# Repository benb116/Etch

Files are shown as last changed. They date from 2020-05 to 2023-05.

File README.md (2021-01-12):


# Etch

Etch is an auto-drawing digital Etch a Sketch built on top of a Raspberry Pi. Stepper motors mounted under a television turn 3D printed knobs to match the drawing motion on the screen. The knobs can also be turned by hand to manually draw on the display.

This repository contains the following:

* 3D models of the shell, knobs, and other support pieces
* Altium PCB design files and Gerber files for the custom circuit boards
* RPi files for the server and motor/sensor integration
* Python scripts for generating art files from images

## About

### Hardware

Etch is built around a Raspberry Pi connected to a TV and two stepper motors. The Pi is connected to a custom breakout board that links with two other custom boards mounted to the back of the motors.

The motor boards serve two functions:

1. **AUTO Mode** - Take in step and direction signals from the breakout board and route them to the onboard stepper driver.
2. **MANUAL Mode** - Sense the orientation of a diametrically polarized magnet on the back of the motor axis. The motor position is then sent to the Pi to monitor the user's input.

The motors, shaft couplers, and knobs are mounted to two brackets that are adhered to the TV. 3D printed shell pieces are connected to an aluminum extrusion frame and wrapped in red vinyl.

Read more about [ME work](https://github.com/benb116/Etch/tree/master/ME) and [EE work](https://github.com/benb116/Etch/tree/master/EE).

### Software

The Pi runs a Python webserver that integrates with the motors and sensors. The server communicates with a webpage running in a browser that is displayed on the screen. A websocket connection passes information back and forth about art data, timing, and user input. In AUTO Mode, the server also runs through a script of artwork to display.

Art files contain the lists of points in order of travel. They also include information about drawing speed and knob rotation rates. These files can be generated with different methods:

* [ImageGen.py](https://github.com/benb116/Etch/blob/master/Art/ImageGen.py) - Take a full image and generate a path that traces contours and fills in darker regions.
* [PathFinder.py](https://github.com/benb116/Etch/blob/master/Art/pathfinder.py) - Identifies the path in a single line drawing
* DIY - You can use any method that outputs a series of line segments

Read more about the [Pi](https://github.com/benb116/Etch/tree/master/rPi) code and [Art](https://github.com/benb116/Etch/tree/master/Art) code.

## Further work

### Hardware

- [ ] Upgrade and fix the custom PCBs
- [ ] Add user input to toggle between AUTO and MANUAL

### Software

- [ ] Improve artwork generation algorithms
- [ ] Develop a show script
- [ ] Add support for arcs and splines
- [x] Improve webpage performance
- [x] Create standalone site with artwork

### Artwork

- [ ] Integrate Open Street Map
- [ ] Math and geometry
- [ ] Add support for different hatching schemes

## Acknowledgements

A big thanks to many people and organizations for their help and advice on this project.

* Everyone at [Bresslergroup](https://www.bresslergroup.com/), especially John, Jason, Steve, Nick, and Mike
* [Evil Mad Scientist](https://wiki.evilmadscientist.com/StippleGen)
* [Andrew Brooks](https://brooksandrew.github.io/simpleblog/articles/intro-to-graph-optimization-solving-cpp/)
* [Sunny Days](http://sunnybala.com/2018/09/10/python-etch-a-sketch.html)
* [Adrian Rosebrock](https://www.pyimagesearch.com/2015/04/06/zero-parameter-automatic-canny-edge-detection-with-python-and-opencv/)
* [Joe Freeman](https://web.archive.org/web/20140918131540/http://joefreeman.co.uk/blog/2009/09/lineographic-interpretations-of-images-with-an-etch-a-sketch/)
* [MIT](http://web.mit.edu/urban_or_book/www/book/chapter6/6.4.4.html)

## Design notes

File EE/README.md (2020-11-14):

# Electrical Hardware

Along with a Raspberry Pi, Etch utilizes two unique custom PCBs to route signals and power to various components.

1. Motor Board - Mounted to the back of each stepper motor, this PCB has a stepper motor driver to control the knob and a magnetic encoder to read the knob's position.
2. Breakout board - Mounted in the center of the TV, this PCB routes signals from the Pi to the correct board. It also distributes motor power.

## Motor Board
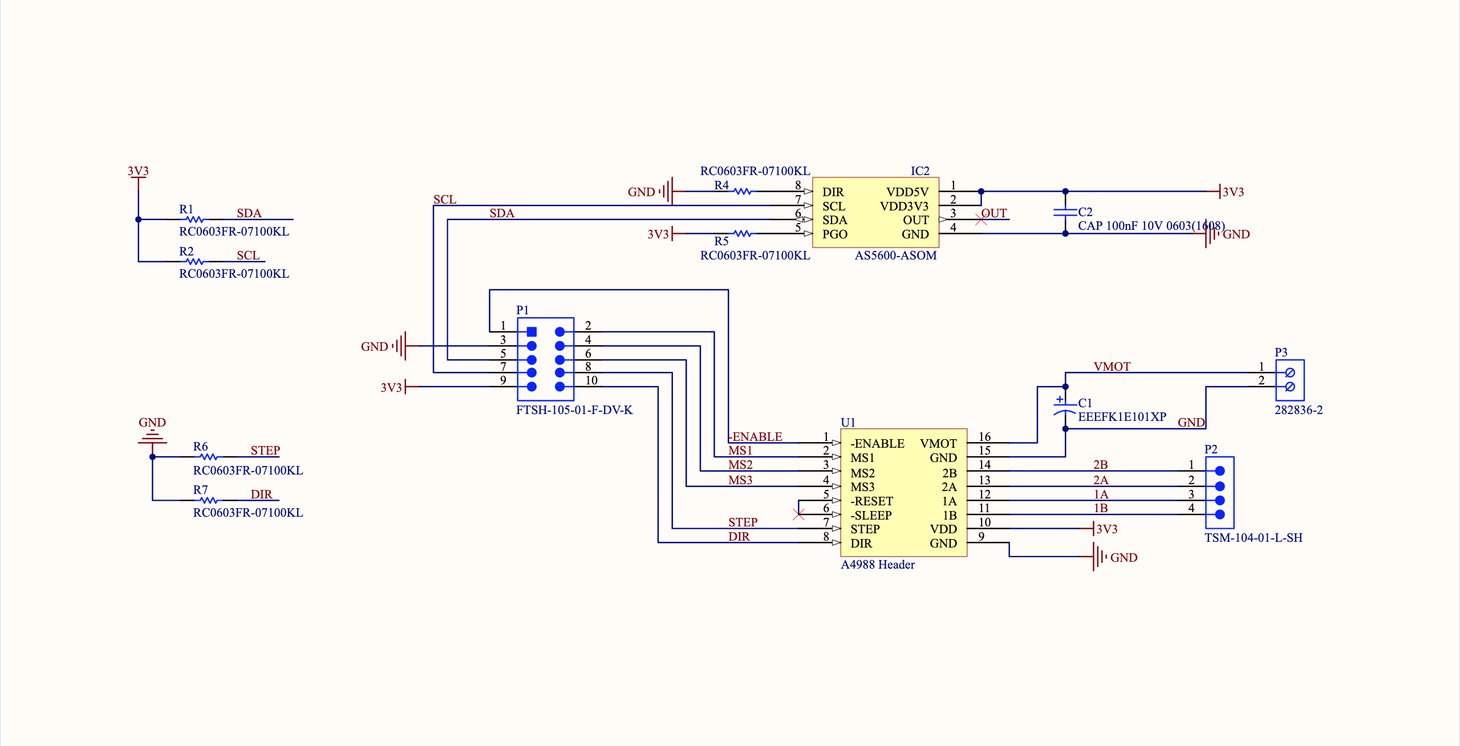
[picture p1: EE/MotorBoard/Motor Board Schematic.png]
Schematic


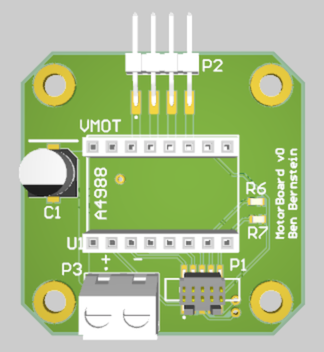
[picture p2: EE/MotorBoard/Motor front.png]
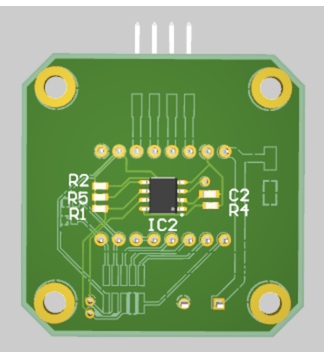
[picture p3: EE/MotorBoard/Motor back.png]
RenderBack


The Motor Board is designed to fit on the back of a standard NEMA-17 stepper motor. It accepts power and a 10-pin signal cable from the Breakout Board. The signals are:

1. **-ENABLE** | *Active low* | Pull this pin high to disable the motor (used in MANUAL mode)
2. **MS1** | *Pulled low* | Microstepping control pin 1
3. **GND**
4. **MS2** | *Pulled low* | Microstepping control pin 2
5. **SDA** | *Pulled high* | Encoder I2C Data pin
6. **MS3** | *Pulled low* | Microstepping control pin 3
7. **SCL** | *Pulled high* | Encoder I2C Clock pin
8. **STEP** | *Pulled low* | Step pulse pin
9. **3v3**
10. **DIR** | *Pulled low* | Direction control pin

Along with support components and connectors, the PCB has two main parts:

1. Headers that match an A4988 stepper motor driver (or similar) on the top layer
2. An [AS5600 magnetic rotary position sensor](https://ams.com/as5600) on the bottom layer. The sensor is centered over the motor axle which has a [diametrically polarized magnet](https://www.kjmagnetics.com/magdir.asp) glued to it. As the motor turns, the magnetic field rotates and is read by the sensor.
	- Note: Data is read from the sensor over I2C. The sensor has a fixed I2C address, so a 2-channel i2c bus multiplexer is required (see Breakout Board)

## Breakout Board
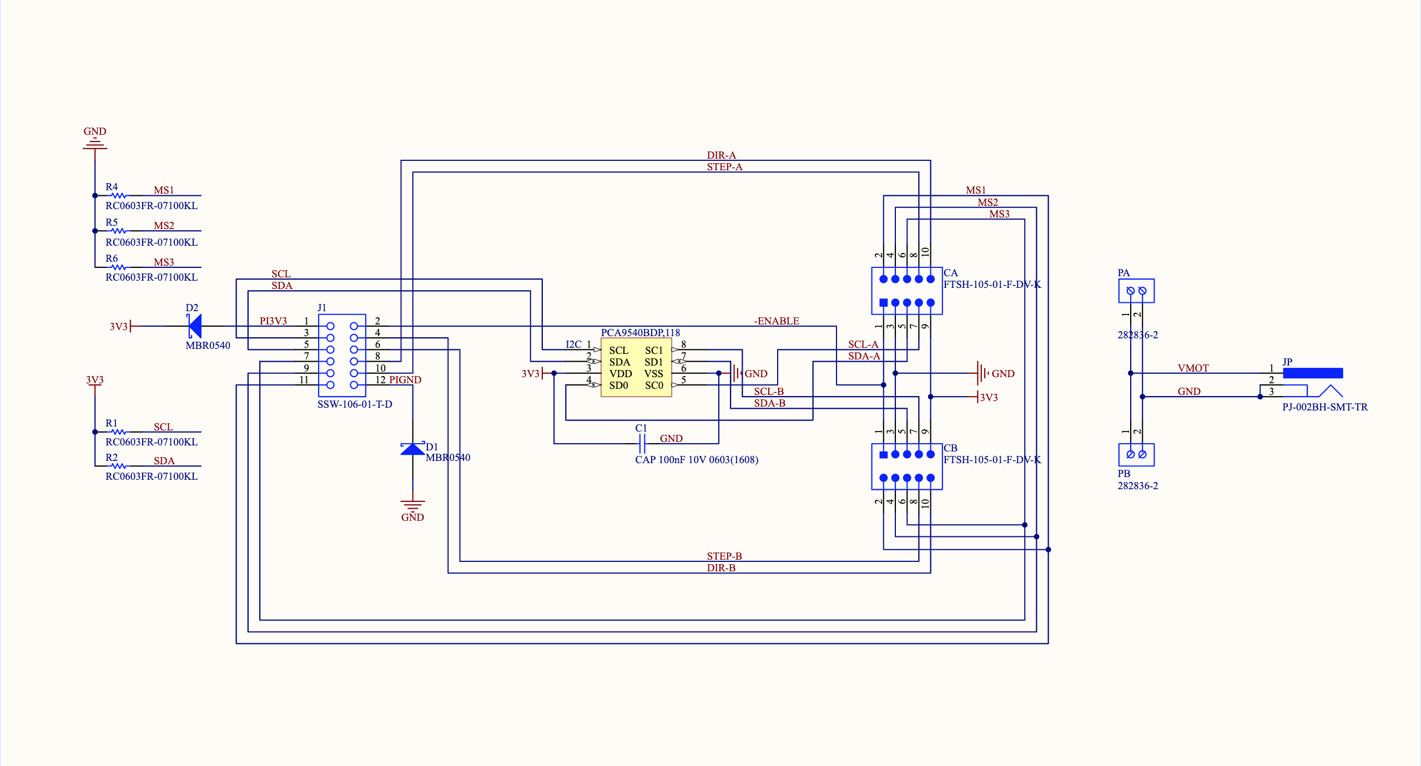
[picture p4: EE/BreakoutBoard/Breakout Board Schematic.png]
Schematic


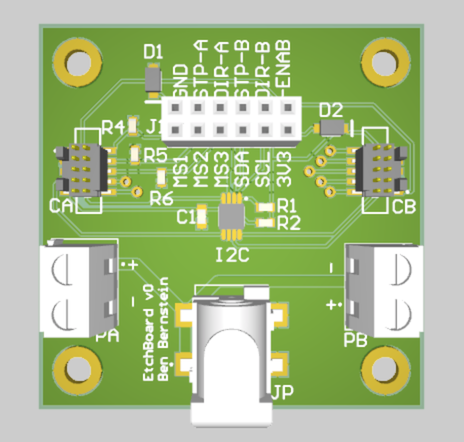
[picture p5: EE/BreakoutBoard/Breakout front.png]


The Breakout Board mainly routes signals and power between the Pi and the two Motor Boards. It accepts power from a DC jack and 12 signals from the Pi via jumper cable:

| Pin Name | Hi / Lo | Description | Connect to RPi Pin 
| --- | --- | --- | --- |
| **GND** | | Ground | GND
| **STEPA** | *Pulled low* | Step pulse pin for motor A | GPIO 21 (Pin 40)
| **DIRA** | *Pulled low* | Direction control pin for motor A | GPIO 20 (Pin 38)
| **STEPB** | *Pulled low* | Step pulse pin for motor B | GPIO 26 (Pin 37)
| **DIRB** | *Pulled low* | Direction control pin for motor B | GPIO 19 (Pin 35)
| **-ENABLE** | *Active low* | Pull this pin high to disable the motors (used in MANUAL mode) | GPIO 12 (Pin 32)
| **MS1** | *Pulled low* | Microstepping control pin 1 | GPIO 14 (Pin 8)
| **MS2** | *Pulled low* | Microstepping control pin 2 | GPIO 15 (Pin 10)
| **MS3** | *Pulled low* | Microstepping control pin 3 | GPIO 18 (Pin 12)
| **SDA** | *Pulled high* | Multiplexer I2C Data pin | GPIO 2 (Pin 3)
| **SCL** | *Pulled high* | Multiplexer I2C Clock pin | GPIO 3 (Pin 5)
| **3v3** | | 3.3V from the RPi | 3.3V |

Along with connectors, the Breakout Board has a [PCA9540 2-channel I2C multiplexer](https://www.nxp.com/docs/en/data-sheet/PCA9540B.pdf). Because the AS5600 has a fixed address, the Pi can use the mux to select which sensor to read before pulling the value. This is done by writing the desired channel to a mux register before reading the value.

### Note: The current design has 100k resistors at R1 and R2. These should be 4.7k resistors

## Connectors

The 10-pin connections between Breakout and Motor Boards are sent over [2-foot Samtec cables (FFSD-05-D-24.00-01-N-R)](https://www.samtec.com/products/ffsd-05-d-24.00-01-n-r) to [surface-mount headers (FTSH-105-01-F-DV-K)](https://www.samtec.com/products/ftsh-105-01-f-dv-k). These were chosen because they are compact, long enough, keyed to prevent miswiring, and because free samples are available from the manufacturer. Future versions of the boards will use through-hole connectors which are easier to solder. If there is interest in a general-use Motor Board, the connectors may be swapped for 0.1" pitch connectors to preserve compatibility with existing DIY electronics kits.

## Improvements

- [ ] Fix pull up values
- [ ] Pullup for -ENABLE
- [ ] Get rid of diodes
- [ ] Test points and LEDs
- [ ] New connectors
- [ ] Can move components into the A4988 footprint
- [ ] Change to through hole components when possible
- [ ] Larger SMCs
- [ ] Change the footprint of the PCA9540 (PCA9540BD, not BDP)
- [ ] Accomodate DRV8825? Spec for voltage and current: 45V*1.5, 2.5 A per coil

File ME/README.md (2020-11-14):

# Mechanical Hardware

The CAD for this project was done in OnShape. View the assembly and parts [here](https://cad.onshape.com/documents/a323499ca448ff5cfd3dca22/w/1d5ba33bc2795cecee47b742/e/558a06e23199a00c5437c471).

The sizes and dimensions for many of these parts will depend on the size of the TV. Take measurements of your display and make any necessary adjustments if you plan on adapting these components.

Some notes about specific parts:

* The shell is made from 18 3D printed pieces mounted to an 80/20 frame, then wrapped in a vinyl ashesive sheet. This isn't the best way to make a frame like this, but it was the best way to make one cheaply with the tools I had during quarantine.
* The 80/20 crossbar rests on the top of the TV, and ribs help position the shell on the TV.
* The knobs are 3D printed and designed to not require supports if printed face down. Consider reducing infill and increasing the wall thickness to decrease the print time.
* 3D printed brackets hold the motors to the TV because I did not want the frame or shell to support their weight and forces. Because TVs have no mounting features, the brackets are adhered to the TV using VHB.
* Thin spacer parts separate the Motor Boards from the motors and ensure that the magnetic sensor is correctly spaced.

## Bill of Materials

### Purchased parts

| Item | Price | Qty | Total | Link |
|---|---|---|---|---|
| TV | X | 1 | X |  |
| Raspberry Pi | $45 | 1 | $45 | [https://amazon.com/gp/product/B07JR3M7FY](https://amazon.com/gp/product/B07JR3M7FY) |
| Stepper Motors | $11 | 2 | $22 | [https://amazon.com/gp/product/B00PNEQ9T4](https://amazon.com/gp/product/B00PNEQ9T4) |
| A4988 Drivers | $9 | 1 | $9 | [https://amazon.com/gp/product/B01FFGAKK8](https://amazon.com/gp/product/B01FFGAKK8) |
| DC Power Brick | $16 | 1 | $16 | [https://amazon.com/gp/product/B01ISM267G](https://amazon.com/gp/product/B01ISM267G) |
| Red vinyl wrap | $40 | 1 | $ 40 | [https://amazon.com/gp/product/B01LQIZX6U](https://smile.amazon.com/gp/product/B01LQIZX6U/) |
| 80/20 accessories | $40 | 1 | $ 40 | [https://8020.net/](https://8020.net/) |
| microHDMI to HDMI Adapters | $8 | 1 | $8 | [https://amazon.com/gp/product/B07K21HSQX](https://amazon.com/gp/product/B07K21HSQX) |
| Jumper wires | $6 | 1 | $6 | [https://amazon.com/dp/B01L5UKAPI/](https://amazon.com/dp/B01L5UKAPI/) |
| Board Mount Screws M3 30mm Panhead | $9 | 1 | $9 | [https://amazon.com/dp/B00F33U5S6](https://amazon.com/dp/B00F33U5S6) |
| Bracket Mount Screws M3 10mm Flathead | $6 | 1 | $6 | [https://amazon.com/dp/B01D4VHJJ6](https://amazon.com/dp/B01D4VHJJ6) |
| Coupler Set Screws 4-40 1/8" Set  | $3 | 1 | $3 | [https://amazon.com/dp/B07VM9Z2FS](https://amazon.com/dp/B07VM9Z2FS) |
| Signal Cables | $12 | 2 | $24 | |

### Custom parts
| Item | Qty | Mfg. Method |
|---|---|---|
| Motor Board | 2 | Custom PCB |
| Breakout Board | 1 | Custom PCB |
| Knob Wheel | 2 | Print |
| Shaft Coupler | 2 | Machine |
| Bracket - Left | 1 | Print |
| Bracket - Right | 1 | Print |
| Shell pieces | 18 | Print |
| Aluminum extrusion | 4 | Cut |

## Assembly

1. If you will be wall-mounting the TV, complete that step first.
1. Screw the Motor Boards onto the motors with a board spacer sandwiched between each (8x M3 30mm screws).
2. Screw the motors to the brackets (8x M3 10mm screws). Keep the orientation of the board in mind; the signal and power cables will need to reach the bottom middle of the TV.
3. Attach the two shaft couplers to the motor shafts (2x 4-40 1/8" set screws)
4. Place the brackets onto the bottom of the TV using adhesive. You may need to adjust their position later.
5. Assemble the four aluminum extrusion pieces into a rectangular frame.
5. Screw the shell pieces onto the frame.
6. Fill the gaps between shell pieces if desired.
7. Carefully adhere the vinyl wrap to the shell and frame.
1. Place the shell and frame over the front of the TV so that the shaft couplers fit through the holes.
4. Carefully press the knobs onto the shaft couplers.
5. Mount the RPi and other electronics to the back of the TV using tape or zipties. Connect the RPi to the TV's HDMI port.
6. Connect the signal and power wires from the Breakout Board to the Motor Boards

## Further work
- [ ] Add a button to toggle between AUTO and MANUAL
- [ ] Add a way for user to clear the screen

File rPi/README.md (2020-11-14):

# Raspberry Pi Code

The RPi acts as the brain of the system, directing the motors, receiving user input, and orchestrating and displaying the artwork. It consists of a Python webserver integrated with motor control and I2C data firmware that communicates with a web-based frontend over websockets.

## Webserver

The Pi runs a Flask webserver with websocket capabilities. It has three main functions:

1. Communicate with the front webpage that displays the animated artwork. It does this via websocket communication and serving requests for data JSON files.
2. Send precisely timed step commands to the motors that are synchronized with the art animation (this occurs in AUTO mode).
3. Repeatedly read the position data from both sensors and calculate the corresponding pointer movement (this occurs in MANUAL mode).

## Frontend

The Pi is also connected to the TV and displays a webpage in Chromium. The webpage operates differently based on the mode:

1. In AUTO mode, the page communicates with the server using websockets and AJAX requests to send and receive art data. It then creates an SVG with the data and animates the path being drawn.
2. In MANUAL mode, the page receives websocket "ticks" that tell it to draw horizontally or vertically on a Canvas element.

## Art files

Art data is stored in JSON objects with the following properties:

* Name
* pxSpeed - How fast should the pointer move across the screen (pixels per second)
* pxPerRev - How many pixels to move the pointer for a full knob rotation
* points - an array of points to draw lines between sequentially (each point is [x,y])

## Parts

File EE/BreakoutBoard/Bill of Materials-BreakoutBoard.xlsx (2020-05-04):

Line # | Name | Description | Designator | Revision ID | Revision State | Quantity | Manufacturer 1 | Manufacturer Part Number 1 | Manufacturer Lifecycle 1 | Supplier 1 | Supplier Part Number 1 | Supplier Unit Price 1 | Supplier Subtotal 1
 | CAP 100nF 10V 0603(1608) | CAP 100nF 10V ±10% 0603 (1608 Metric) Thickness 1mm SMD | C1 |  | Unknown server | 1 | KEMET | C0603C104K8RACTU | Volume Production | Digi-Key | 399-1095-6-ND | 0.14 | 0.14
3 | FTSH-105-01-F-DV-K | Male Header, Pitch 1.27 mm, 2 x 5 Position, Height 6.12 mm, RoHS, Tube | CA, CB |  | Unknown server | 2 | Samtec | FTSH-105-01-F-DV-K | Volume Production | Digi-Key | SAM8796-ND | 2.9 | 5.8
4 | MBR0540 | Schottky Rectifier, 40 V, 0.5 A, 2-Pin SOD-123, RoHS, Tape and Reel | D1, D2 |  | Unknown server | 2 | ON Semiconductor / Fairchild | MBR0540 | Volume Production | Digi-Key | MBR0540DKR-ND | 0.33 | 0.66
 | PCA9540BDP,118 | IC I2C MUX 2CH 8-TSSOP | I2C |  | Unknown server | 1 | NXP Semiconductors | PCA9540BDP,118 |  | Digi-Key | 568-1845-1-ND | 1.48 | 1.48
8 | SSW-106-01-T-D | SQ Post Socket, Through-hole, Vertical, -55 to 105 degC, 2.54mm Pitch, 12-Pin, Female, RoHS | J1 |  | Unknown server | 1 | Samtec | SSW-106-01-T-D | Volume Production | Digi-Key | SAM1212-06-ND | 1.01 | 1.01
6 | PJ-002BH-SMT-TR | DC Power Jack, 24 V, -25 to 85 degC, 3-Pin SMD, RoHS, Bulk | JP |  | Unknown server | 1 | CUI | PJ-002BH-SMT-TR | Volume Production | Digi-Key | CP-002BHPJDKR-ND | 1.44 | 1.44
2 | 282836-2 | Female Header, Pitch 5 mm, 1 x 2 Position, Height 10 mm, Tail Length 3.5 mm, Rohs, Bulk | PA, PB |  | Unknown server | 2 | TE Connectivity | 282836-2 | Volume Production | Digi-Key | A98076-ND | 0.71 | 1.42
7 | RC0603FR-07100KL | Chip Resistor, 100 KOhm, +/- 1%, 0.1 W, -55 to 155 degC, 0603 (1608 Metric), RoHS, Tape and Reel | R1, R2, R4, R5, R6 |  | Unknown server | 5 | Yageo | RC0603FR-07100KL | Volume Production | Digi-Key | 311-100KHRCT-ND | 0.023 | 0.23

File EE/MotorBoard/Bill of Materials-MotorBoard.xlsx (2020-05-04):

Line # | Name | Description | Designator | Revision ID | Revision State | Quantity | Manufacturer 1 | Manufacturer Part Number 1 | Manufacturer Lifecycle 1 | Supplier 1 | Supplier Part Number 1 | Supplier Unit Price 1 | Supplier Subtotal 1
1 | EEEFK1E101XP | Aluminum Electrolytic Capacitor, 100 uF, +/- 20%, 25 V, 2-Pin SMD (Size Code D8), -55 to 105 degC, RoHS, Tape and Reel | C1 |  | Unknown server | 1 | Panasonic | EEE-FK1E101XP | Volume Production | Digi-Key | PCE3797DKR-ND | 0.53 | 0.53
 | CAP 100nF 10V 0603(1608) | CAP 100nF 10V ±10% 0603 (1608 Metric) Thickness 1mm SMD | C2 |  | Unknown server | 1 | Vishay Vitramon | VJ0603Y104KXQCW1BC | Volume Production | Digi-Key | 720-1689-6-ND | 0.19 | 0.19
3 | AS5600-ASOM | SENSOR ANGLE 360DEG SMD | IC2 |  | Unknown server | 1 | ams | AS5600-ASOM | Volume Production | Digi-Key | AS5600-ASOMDKR-ND | 3.47 | 3.47
4 | FTSH-105-01-F-DV-K | Male Header, Pitch 1.27 mm, 2 x 5 Position, Height 6.12 mm, RoHS, Tube | P1 |  | Unknown server | 1 | Samtec | FTSH-105-01-F-DV-K | Volume Production | Digi-Key | SAM8796-ND | 2.9 | 2.9
5 | TSM-104-01-L-SH | 0.025" SQ Post Header, Surface Mount, Horizontal, -55 to 125 degC, 2.54 mm Pitch, 4-Pin, Male, RoHS | P2 |  | Unknown server | 1 | Samtec | TSM-104-01-L-SH | Volume Production | Digi-Key | SAM15888-ND | 0.75 | 0.75
6 | 282836-2 | Female Header, Pitch 5 mm, 1 x 2 Position, Height 10 mm, Tail Length 3.5 mm, Rohs, Bulk | P3 |  | Unknown server | 1 | TE Connectivity | 282836-2 | Volume Production | Digi-Key | A98076-ND | 0.71 | 0.71
7 | Custom item 1 |  | P4, P5 |  | Unknown server | 2 | Samtec | SSW-108-01-G-S | Volume Production | Digi-Key | SAM1209-08-ND | 1.36 | 2.72
8 | RC0603FR-07100KL | Chip Resistor, 100 KOhm, +/- 1%, 0.1 W, -55 to 155 degC, 0603 (1608 Metric), RoHS, Tape and Reel | R1, R2, R4, R5, R6, R7 |  | Unknown server | 6 | Yageo | RC0603FR-07100KL | Volume Production | Digi-Key | 311-100KHRCT-ND | 0.023 | 0.23
 | A4988 Header | Female Header pins for the A4988 Motor Driver Carrier | U1 |  | Unknown server | 1 | Harwin | M20-7820842 | Volume Production | Digi-Key | 952-1823-ND | 1.1 | 1.1

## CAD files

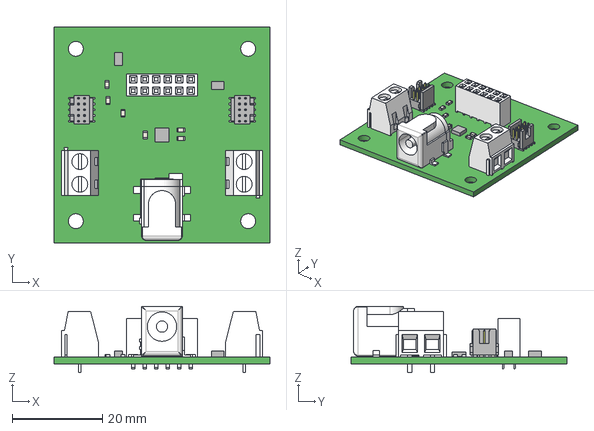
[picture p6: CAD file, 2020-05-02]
EE/BreakoutBoard/BreakoutBoard.step
47.8 x 47.8 x 14.7 mm

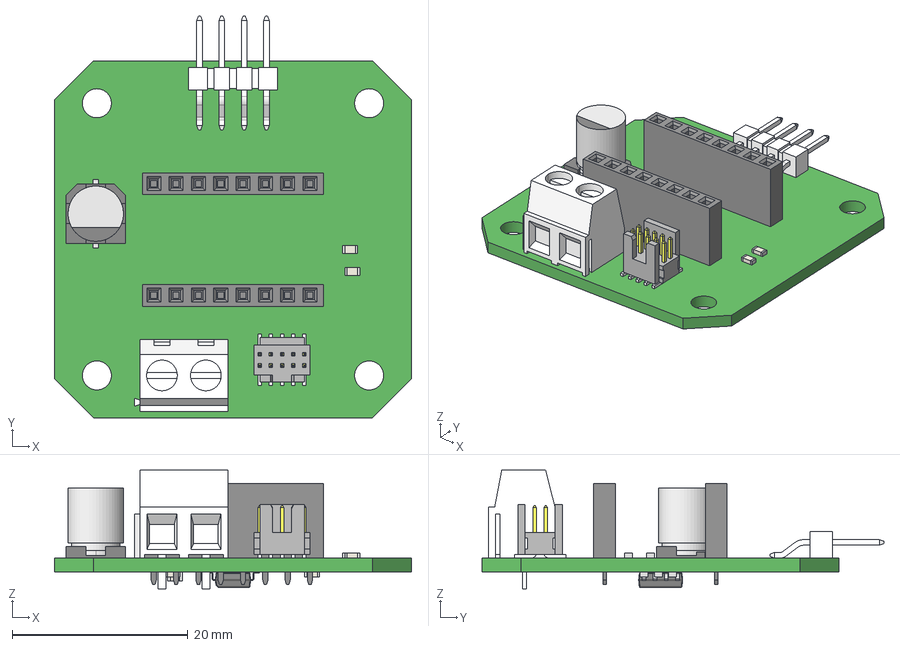
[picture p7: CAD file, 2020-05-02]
EE/MotorBoard/MotorBoard.step
40.6 x 45.7 x 13.5 mm

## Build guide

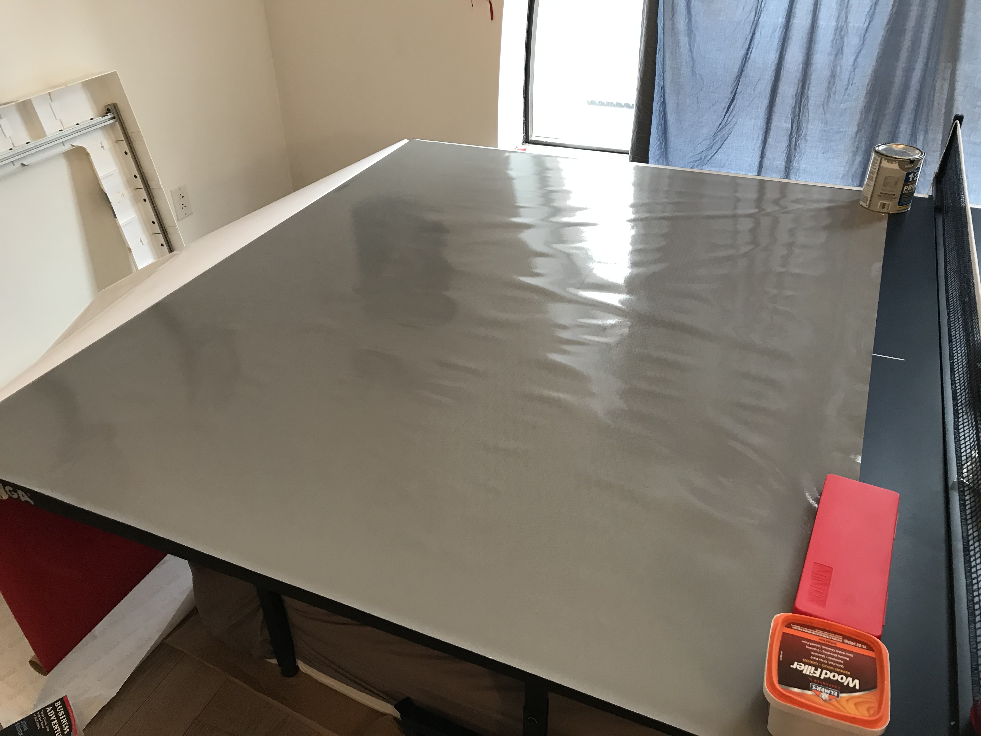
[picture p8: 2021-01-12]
media/Build Album/18 - C22E1oS.jpg

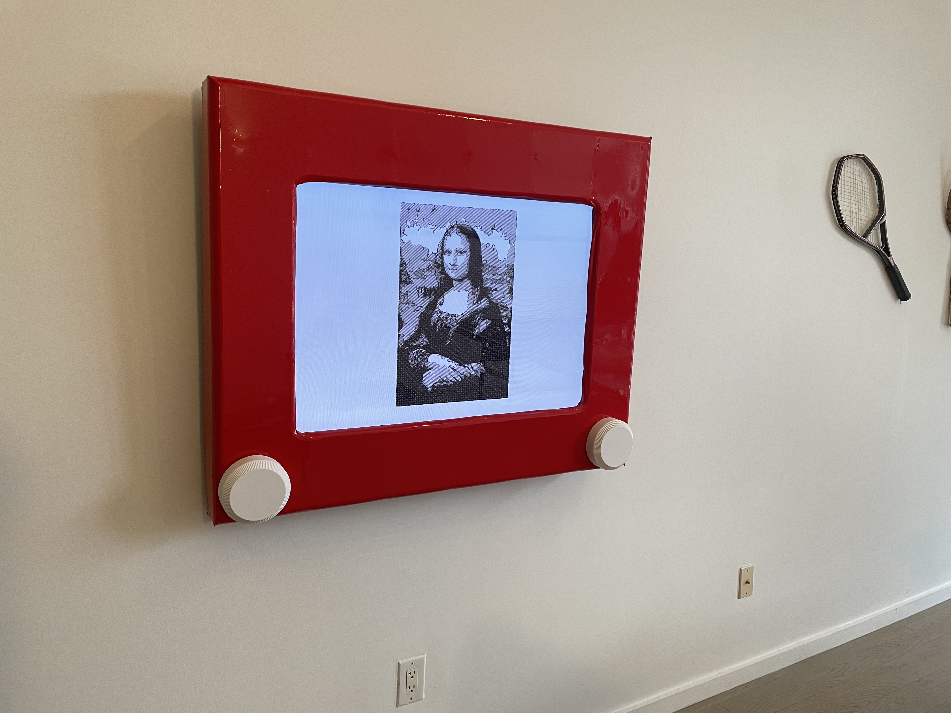
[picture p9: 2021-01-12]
media/Build Album/01 - c40cEE7.jpg

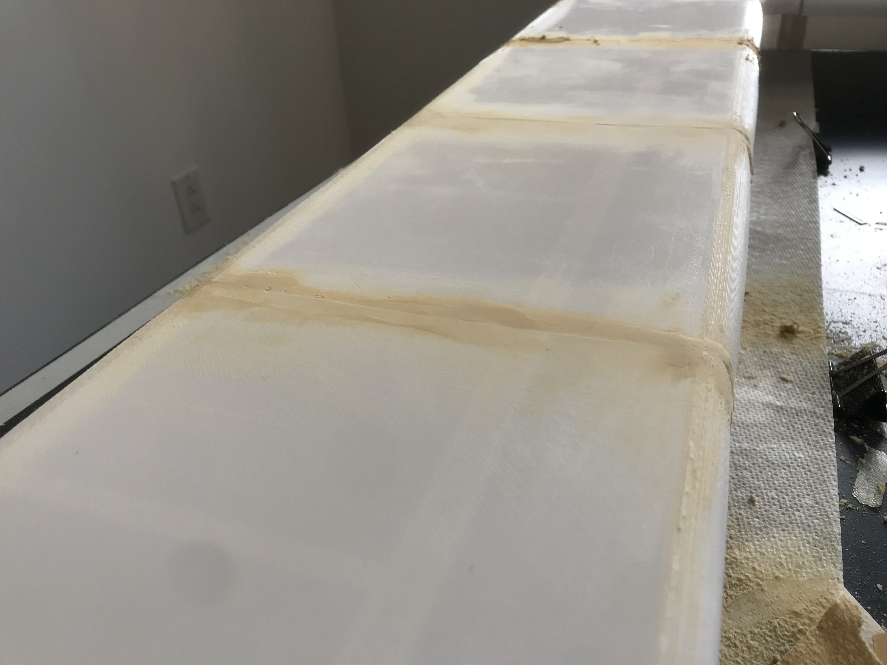
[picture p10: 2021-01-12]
media/Build Album/17 - L3NqXKR.jpg

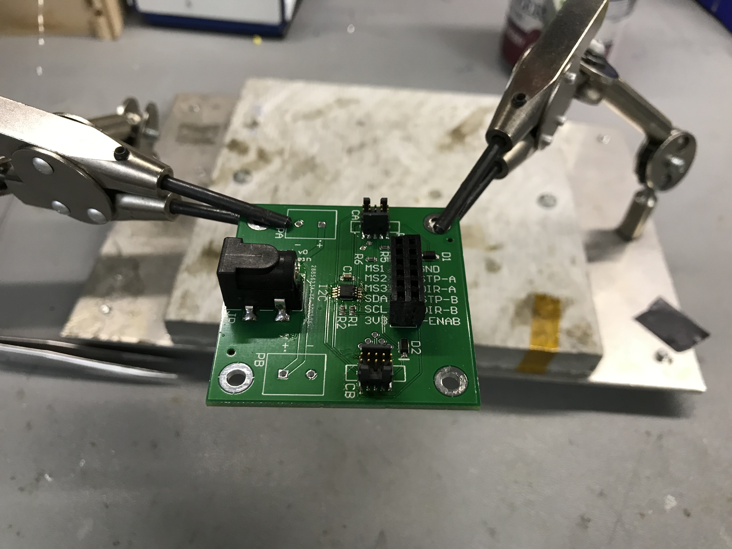
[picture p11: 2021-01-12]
media/Build Album/05 - YKPvkfG.jpg

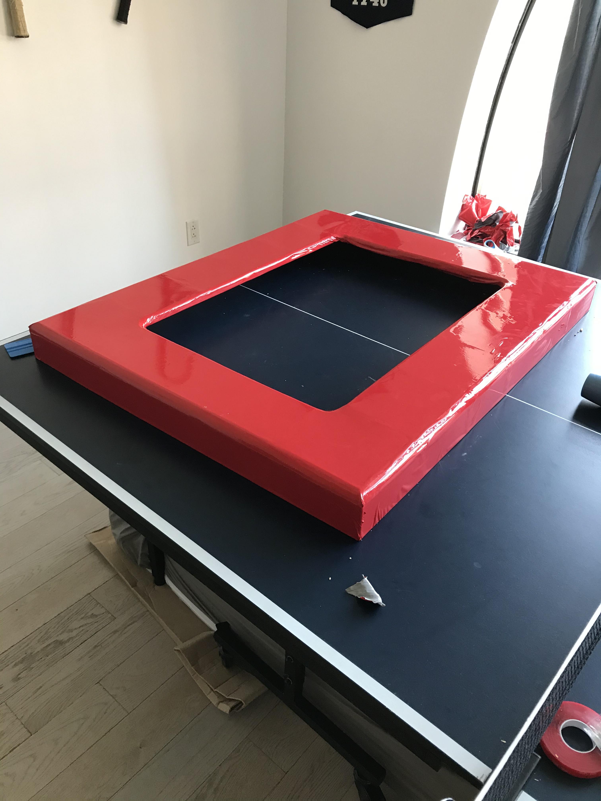
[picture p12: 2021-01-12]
media/Build Album/21 - bCa3hBD.jpg

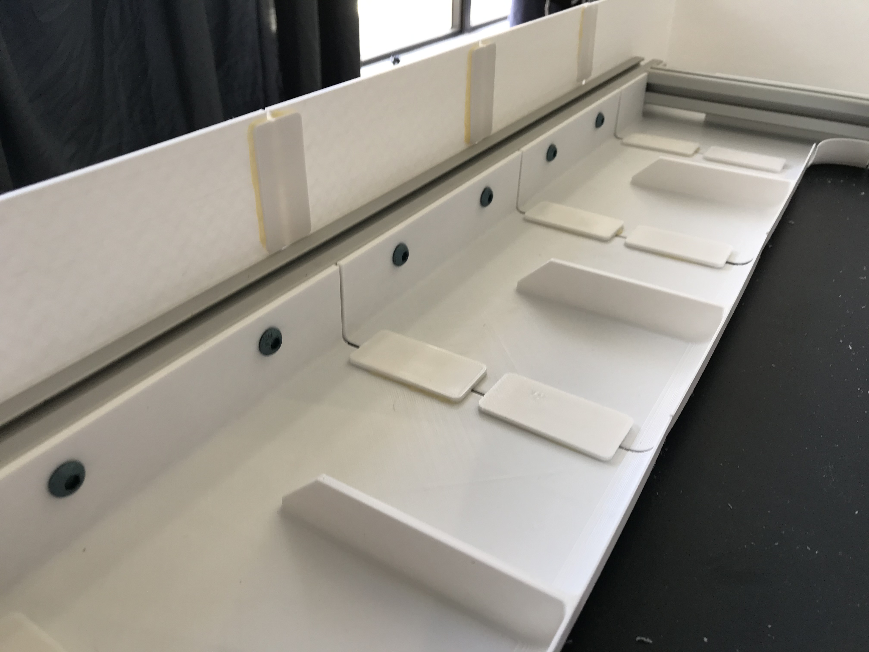
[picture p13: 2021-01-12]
media/Build Album/15 - 7K4GJ1A.jpg

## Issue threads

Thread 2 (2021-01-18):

opening browser external to rPi

dlarue, 2021-01-18:
Looks like a fun project and love the effort to make it looks like a BIG ETCH-a-Sketch.

I was playing with the code a bit and trying to figure out installation and how it works when I noticed I could not connect to the server on the rPi from my desktop. Learned a bit about Flask....

I did get the client to run from my desktop with this in server.py:
        #socketio.run(app)
        socketio.run(app, host='0.0.0.0', port=5000, debug=True)

I also changed the two references to "localhost" in public/art/index.html to the hostname of my rPi.

Now if I can only solve the  socketio version error the server spits out:
The client is using an unsupported version of the Socket.IO or Engine.IO protocols (further occurrences of this error will be logged with level INFO)

benb116, 2021-01-18:
Hi Doug, not sure what might be causing that error. For reference, I am using python 3.8 and flask-socketio version 4.3.1. The frontend is pulling the v2 socket-io library. Which versions of these various libraries are you using? See [Here](https://github.com/miguelgrinberg/Flask-SocketIO/issues/1426) for a possible solution. Also please see [This](https://flask-socketio.readthedocs.io/en/latest/#version-compatibility) to make sure your SocketIO library is compatible with the flask-socketIO library.

dlarue, 2021-01-18:
I downgraded the flask-socketio lib to 3.0.0 and the error disappeared. I was then getting origin errors so I added this to accept all origins and that error went away:
#DJL socketio = SocketIO(app)
socketio = SocketIO(app,cors_allowed_origins="*")

I just can't get it to render anything. My web page is all gray but for a little text box in the upper left side and a Fast check box.
I type Homer into the box and hit enter and nothing happens and the server spits out the following with no change on the client:
(env) pi@dougs-audiobot:~/Etch/rPi $ python server.py
begin
begin
(1110) wsgi starting up on http://0.0.0.0:5000
(1110) accepted ('192.168.68.116', 59212)
192.168.68.116 - - [18/Jan/2021 14:09:52] "GET /socket.io/?EIO=3&transport=polling&t=NSNZ1HD HTTP/1.1" 200 429 0.004047
(1110) accepted ('192.168.68.116', 59214)
192.168.68.116 - - [18/Jan/2021 14:09:52] "GET /socket.io/?EIO=3&transport=polling&t=NSNZ1Iy&sid=9a9841431bd74feab0e9f511e3f96cd1 HTTP/1.1" 200 246 0.001782
192.168.68.116 - - [18/Jan/2021 14:09:52] "GET /socket.io/?EIO=3&transport=polling&t=NSNZ1JI&sid=9a9841431bd74feab0e9f511e3f96cd1 HTTP/1.1" 200 246 0.001304
(1110) accepted ('192.168.68.116', 59220)
art/Homer.json
192.168.68.116 - - [18/Jan/2021 14:10:00] "GET /art/Homer.json HTTP/1.1" 200 9140 0.005085

pip list on the rpi:
(env) pi@dougs-audiobot:~/Etch/rPi $ pip list
Package         Version
--------------- ---------
bidict          0.21.2
certifi         2018.8.24
chardet         3.0.4
click           7.1.2
dnspython       1.16.0
eventlet        0.30.0
Flask           1.1.2
Flask-Ext       0.1
Flask-SocketIO  3.0.0
gpio            0.3.0
greenlet        1.0.0
idna            2.6
itsdangerous    1.1.0
Jinja2          2.11.2
MarkupSafe      1.1.1
netifaces       0.10.6
pi-utils        0.0.1
pip             20.3.3
pkg-resources   0.0.0
python-apt      1.8.4.3
python-engineio 3.14.2
python-socketio 5.0.0
requests        2.21.0
setuptools      3.3
six             1.12.0
socketio        0.2.1
ssh-import-id   5.7
urllib3         1.24.1
virtualenv      15.1.0
Werkzeug        1.0.1
wheel           0.36.2

benb116, 2021-01-18:
That seems correct for the server side of things. Could you attempt to run this again with the DevTools console open on the frontend browser? The output should look like this:

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

If your console looks the same, I would add some print statements to [this](https://github.com/benb116/Etch/blob/212a8fec2dea0faf8f2097965b56690204802905/rPi/server.py#L89) function. This should be called once the frontend is finished its setup. See if those print statements are triggered. I wonder if there is still some websockets issues between client and server.

benb116, 2021-01-18:
Actually, I just realized that the server is not printing "connected" in your log. That is likely the gating issue. I'm not sure what could cause that though.

dlarue, 2021-01-18:
Using that developer tools window, I saw some errors listed and it looks like it is still still an orgin issue:

2
(index):1 Access to fetch at 'http://192.168.68.122:5000/art/Homer.json' from origin 'http://dougs-audiobot.local:5000' has been blocked by CORS policy: No 'Access-Control-Allow-Origin' header is present on the requested resource. If an opaque response serves your needs, set the request's mode to 'no-cors' to fetch the resource with CORS disabled.

dlarue, 2021-01-18:
as mentioned by the error message I added mode: 'no-cors' to the public/index.html file and no more errors shown from developemnt tools screen. But still no rendering when I enter Homer.

        fetch('http://dougs-audiobot.local:5000'+url, {cache: 'reload'},{ mode: 'no-cors'})

Should I be seeing just a gray screen with that one test input box and check box? I really don't know what this is supposed to look like and was quite surprised the server.py code wasn't erroring out without a GPIO package, etc. I've connected no motor or encoder hardware yet. Just trying to get the screen to render the default designs.

benb116, 2021-01-19:
At first the gray screen (and the input box and check box) should be all that is visible. Once you type in "Homer" and press enter, then the animation should start after about a second. There is code in the server file that only imports the GPIO package if the code is running on an rPi; if it isn't, then motor and sensor integration are not loaded.

It looks like the frontend is correctly getting the data from the backend. At this point, I'd guess the issue lies in the "on_clientArtReady" function running in the server. When the frontend has set everything up (which it has in your case), it sends a message over the socket to the server with the "clientArtReady" tag.

Could you try adding some print statements to that function and see how far the server makes it through? When the server is finished, it should emit a "startTime" event to the client.

dlarue, 2021-01-19:
I have been chasing down the "on_connect" method and how it's not getting called and printing. Went into public/index.html where it creates the socket and that is where the problem seems to be. No socket is getting connected. I added a log of the socket and looked in dev tools to expand the object and see "connected: false" so it's not creating the socket it would seem.
It looks to be creating the data just can't send it to the client for rendering...

print/debug added to public/index.html

   console.log('Pre-Connect');
    var socket = io.connect('http://localhost:5000');
    console.log(socket);
    socket.on('connect', function() {
        console.log('Connected');
    });

benb116, 2021-01-19:
That's certainly odd. I'm afraid I'm at a loss for how to resolve the socket issue.

However, there is a workaround if you'd just like to play around with the display (i.e. without any motor/sensor integration): Immediately after [this line](https://github.com/benb116/Etch/blob/212a8fec2dea0faf8f2097965b56690204802905/rPi/public/index.html#L120) in the frontend code, add `Begin();` this will short-circuit the socket messages being sent and simply start drawing immediately.

Sorry I can't be of more help with regard to the socket error; I'll keep playing around with it.

dlarue, 2021-01-19:
Thanks, the addition of Begin() does start the client rendering.  I will try booting a Ubuntu 20.04 image and see if it works there with later python versions even though I'm running python 3.9. I suspect it's socketio version problems.

dlarue, 2021-01-19:
On Lubuntu 20.04 all it took was this:
sudo apt install git python3-pip python3-socketio python3-flask-socketio python3-eventlet

I tried setting up using pip3 but I got client socket version issues again. Going all native worked and here is what the package versions played out to be using the native install listed above:

ubuntu@ubuntu:~/Etch/rPi$ pip3 list
Package                 Version
----------------------- -------------
apt-xapian-index        0.49
blinker                 1.4  
certifi                 2019.11.28
chardet                 3.0.4
Click                   7.0  
colorama                0.4.3
command-not-found       0.3  
cryptography            2.8  
cupshelpers             1.0  
dbus-python             1.2.16
defer                   1.0.6
distro                  1.4.0
distro-info             0.23ubuntu1
dnspython               1.16.0
entrypoints             0.3  
eventlet                0.25.1
Flask                   1.1.1
Flask-SocketIO          4.2.1
galternatives           1.0.6
greenlet                0.4.15
httplib2                0.14.0
idna                    2.8  
itsdangerous            1.1.0
Jinja2                  2.10.1
keyring                 18.0.1
language-selector       0.1  
launchpadlib            1.10.13
lazr.restfulclient      0.14.2
lazr.uri                1.0.3
lubuntu-update-notifier 0.1  
MarkupSafe              1.1.0
monotonic               1.5  
netifaces               0.10.4
oauthlib                3.1.0
olefile                 0.46
pexpect                 4.6.0
Pillow                  7.0.0
pip                     20.0.2
pycairo                 1.16.2
pycups                  1.9.73
PyGObject               3.36.0
pyinotify               0.9.6
PyJWT                   1.7.1
pymacaroons             0.13.0
PyNaCl                  1.3.0
pyOpenSSL               19.0.0
PyQt5                   5.14.1
python-apt              2.0.0
python-debian           0.1.36ubuntu1
python-engineio         3.11.1
python-socketio         4.4.0
pyxdg                   0.26
PyYAML                  5.3.1
reportlab               3.5.34
requests                2.22.0
requests-unixsocket     0.2.0
SecretStorage           2.3.1
setuptools              45.2.0
simplejson              3.16.0
sip                     4.19.21
six                     1.14.0
systemd-python          234  
ubuntu-advantage-tools  20.3
ubuntu-drivers-common   0.0.0
ufw                     0.36
unattended-upgrades     0.1  
urllib3                 1.25.8
usb-creator             0.3.7
wadllib                 1.3.3
Werkzeug                0.16.1
wheel                   0.34.2
xkit                    0.0.0
ubuntu@ubuntu:~/Etch/rPi$

Closed 2021-11-16.

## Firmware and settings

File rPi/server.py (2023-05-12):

#! python3
from enum import auto
from flask import Flask
from flask_socketio import SocketIO, emit
import time
import threading
from multiprocessing import Process
import json
import sys
import logging
import eventlet

from integration.pi_utils import IsRPi

log = logging.getLogger('werkzeug')
log.setLevel(logging.ERROR)
eventlet.monkey_patch()

AUTO = False

# Dummy functions that are overwritten if on rPi
def readAngle(m):
    pass


def genThreads(a, b, c, d):
    print('pass')
    pass


def motorsOn(bool):
    pass

from integration.auto import genThreads

# Are we running on the rPi
onboard = False
# Want to be able to run the server off the Pi, but local doesn't have libraries
if IsRPi():
    onboard = True
    from RPi import GPIO
    GPIO.setwarnings(False)
    GPIO.setmode(GPIO.BCM)
    from integration.encoder import readAngle
    from integration.motors import motorsOn
    motorsOn(False)

app = Flask(__name__, static_folder='public')
app.config['SEND_FILE_MAX_AGE_DEFAULT'] = 0
app.config['SECRET_KEY'] = 'secret!benwashere'
socketio = SocketIO(app)


# Serve static files
@app.route('/')
def root():
    return app.send_static_file('index.html')


@app.route('/canvas.html')
def root2():
    return app.send_static_file('canvas.html')


@app.route('/socket.io.js')
def socketioFile():
    return app.send_static_file('socket.io.js')


# Socket stuff
@socketio.on('connect')
def on_connect():
    print('connected')


# AUTO MODE #
# Send an art file
@app.route('/art/<path:path>')
def send_art(path):
    print('art/'+path)
    return app.send_static_file('art/'+path)


# After the frontend has downloaded and precomputed the points, it emits a "clientArtReady" message
@socketio.on('clientArtReady')
def on_clientArtReady(url):
    global AUTO
    # pull file that we sent
    AUTO = True
    print('AUTO')
    with open('public/'+url) as json_file:
        data = json.load(json_file)
        points = data['points']
        pxSpeed = data['pxSpeed']
        pxPerRev = data['pxPerRev']

    # Determine unix start time
    # The front and backends will attempt to start the drawing at the same timestamp
    TS = time.time() + 0.5
    # Begin stepping at the start time
    emit('startTime', TS)
    if onboard:
        t = threading.Thread(target=genThreads, args=(points, TS, pxSpeed, pxPerRev))
        t.start()
        t.join()
        resetAngle()
        AUTO = False
        print('MANUAL')

    # Tell the client when the start time is


# MANUAL MODE #
oldVal = [0, 0]


def InitManual():
    global AUTO

    if not onboard:
        return
    # Read initial values from sensors
    resetAngle()

    while True:
        eventlet.sleep(0.01)
        if not AUTO:
            checkTick(0)
            checkTick(1)


def resetAngle():
    oldVal[0] = readAngle(0)
    oldVal[1] = readAngle(1)


# Check if a motor position has changed
def checkTick(mn):
    bitsPerStep = 10
    o = oldVal[mn]
    n = readAngle(mn)
    diff = (n - o)
    # If the diff is > half a rotation, assume it was less than half the other way
    if abs(diff) > 4096/2:
        diff = diff + 4096 * (-1 + 2*(o > n))
    # If above some threshold for a tick
    if abs(diff) >= bitsPerStep:
        # Emit a tick event to the frontend
        socketio.emit('tick', (mn, round(diff/bitsPerStep)))
        print('tick ' + str(mn) + ' ' + str(round(diff/bitsPerStep)))
        oldVal[mn] = n


if IsRPi():
    eventlet.spawn(InitManual)

if __name__ == '__main__':
    print('begin')
    try:
        socketio.run(app)
    finally:
        # Turn off motors on exit
        motorsOn(False)
        if IsRPi():
            GPIO.cleanup()
        sys.exit(0)

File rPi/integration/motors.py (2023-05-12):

import RPi.GPIO as GPIO
import pigpio
import time
GPIO.setmode(GPIO.BCM)
PIGPIO = pigpio.pi()


# Microstepping resolution mapping to select pins hi or lo
resolution = {'Full': (0, 0, 0),
              'Half': (1, 0, 0),
              '1/4': (0, 1, 0),
              '1/8': (1, 1, 0),
              '1/16': (1, 1, 1)}
MODE = resolution['1/16']

pEnab = 7 # Enable pin
pRes = (14, 15, 17) # Microstep resolution pins

pStp1 = 12 # Motor 1 step pin
pDir1 = 20 # Motor 1 direction pin
pStp2 = 13 # Motor 2 step pin
pDir2 = 6  # Motor 2 direction pin

GPIO.setup(pEnab, GPIO.OUT)
GPIO.setup(pRes, GPIO.OUT)
GPIO.setup(pStp1, GPIO.OUT)
GPIO.setup(pDir1, GPIO.OUT)
GPIO.setup(pStp2, GPIO.OUT)
GPIO.setup(pDir2, GPIO.OUT)

PIGPIO.set_mode(pStp1, pigpio.ALT5)
PIGPIO.set_mode(pStp2, pigpio.ALT5)

GPIO.output(pEnab, 0)
GPIO.output(pRes, 0)
GPIO.output(pStp1, 0)
GPIO.output(pDir1, 0)
GPIO.output(pStp2, 0)
GPIO.output(pDir2, 0)

stepdelay = 0.0002

# Turn the motors on or off using the enable pin
def motorsOn(on):
    GPIO.output(pEnab, 1-on) # Active low
    if not on:
        setDirAndFreq(0, 0, 0)
        setDirAndFreq(1, 0, 0)

# Set the microstepping resolution
def setRes(res):
    MODE = resolution[res]
    GPIO.output(pRes, resolution[res])

# Send a single step command to a motor in a direction
def step(mn, mdir):
    # print(mn, mdir)
    msPin = pStp1 if mn == 1 else pStp2
    mdPin = pDir1 if mn == 1 else pDir2
    GPIO.output(mdPin, 1 if mdir == 1 else 0)
    GPIO.output(msPin, 1)
    time.sleep(stepdelay)
    GPIO.output(msPin, 0)
    time.sleep(stepdelay)

# Set up PWM at 50% duty and a certain direction and frequency
def setDirAndFreq(mn, mdir, freq):
    msPin = pStp1 if mn == 1 else pStp2
    mdPin = pDir1 if mn == 1 else pDir2
    GPIO.output(mdPin, 1 if mdir == 1 else 0)
    if freq == 0:
        PIGPIO.write(msPin, 0)
        return
    PIGPIO.hardware_PWM(msPin, freq, 500000)

# Return the total number of steps in one revolution based on the current microstep resolution
def stepsPerRev():
    exp = MODE[2]*4 + MODE[1]*2 + MODE[0]
    if exp == 7:
        exp = 4
    return 200 * 2**exp

setRes('1/16')

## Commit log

2019-06-22 Threading improvements
2019-09-08 Big push
    [bat.csv]
2020-01-05 Motor control and FPS management
2020-05-04 EE build files
    [Bill of Materials-BreakoutBoard.xlsx, Bill of Materials-MotorBoard.xlsx, Pick Place for BreakoutBoard.csv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]
2020-12-12 PWM actually works
2022-04-20 rPi fixes and tweaks
    [auto.py, motors.py, server.py]
